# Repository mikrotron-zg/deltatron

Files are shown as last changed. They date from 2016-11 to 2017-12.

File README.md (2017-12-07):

# Deltatron v1.1
Deltatron is Kossel Mini RepRap 3D Printer variant by [DIYkits.eu](http://www.diykits.eu/). This is version 1.1 of Deltatron in which we switched from J-Head to E3D v6 Lite hotend. For other versions please check _Git tags_ or _GitHub releases_.

This repository includes all 3D printable parts, Marlin firmware ready for upload, and last but not least - assembly and user manuals in Croatian and (eventually) in English.

**New in version 1.1:**
* E3D v6 Lite hotend instead of J-Head
* changed hotend mount, print cooling fan mount and z-probe models to fit new hotend
* changed bed bracket and ramps bracket models, added support for models where needed
* updated assembly manual and added assembly manual for E3D Lite hotend (both in Croatian only)
* changed Configuration.h in Marlin firmware to reflect the hardware changes

## --- **Croatian**

Deltatron je varijanta Kossel Mini RepRap 3D printera - kit možete kupiti u [DIYkits.eu web dućanu](http://www.diykits.eu/shophr/). Ovo je verzija 1.1 Deltatron kita, koja umjesto J-Heada koristi E3D v6 Lite ispisnu glavu (hotend). Starije verzije dostupne su putem _Git tagova_ ili u GitHub repozitoriju pod _releases_.

U ovom repozitoriju nalaze se 3D modeli svih dijelova koji se mogu isprintati 3D printerom, Marlin firmware prilagođen ovome kitu, kao i upute za sastavljanje i korištenje Deltatrona na hrvatskom.

**Novosti u verziji 1.1:**
* J-Head ispisna glava zamjenjena je za E3D v6 Lite hotend
* izmjenjeni modeli za pričvršćenje hotenda, ventilatora za hlađenje printa i z probe
* izmjenjeni modeli držača elektronike i podloge za printanje, gdje je bilo potrebno dodana je potpora za 3D print u modele
* ažurirane su upute za sastavljanje Deltatrona i dodane su upute za sastavljenje E3D Lite6 hotenda
* promjenjene postavke u Configuration.h datoteci Marlin firmware-a u skladu s hardverskim izmjenama

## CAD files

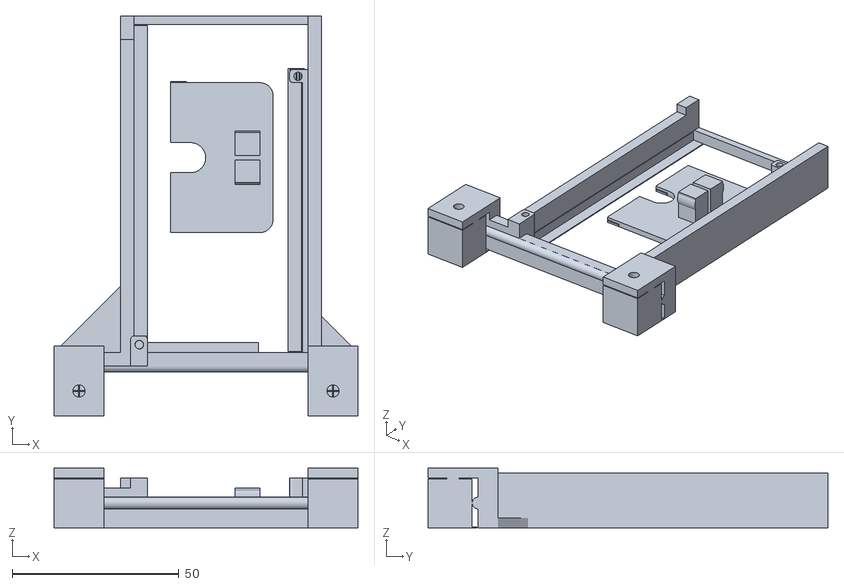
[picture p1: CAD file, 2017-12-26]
model/plate04_support.stl
91.2 x 120.0 x 18.0

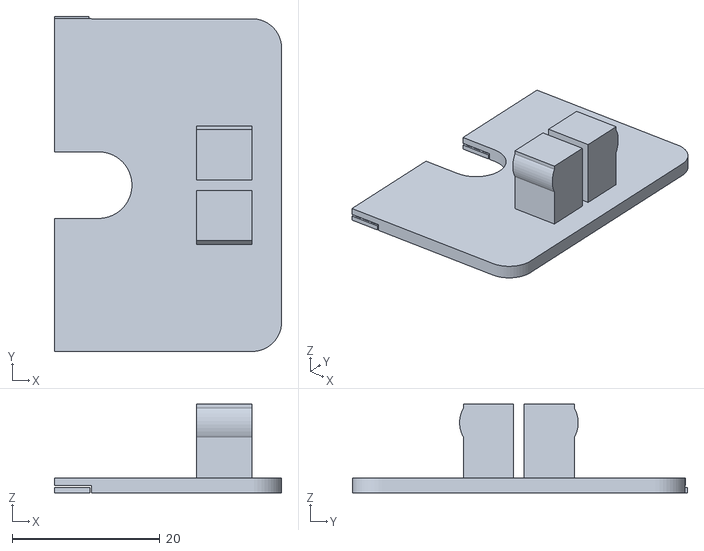
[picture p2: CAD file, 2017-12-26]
model/connector_plate_power.stl
30.8 x 45.3 x 12.0

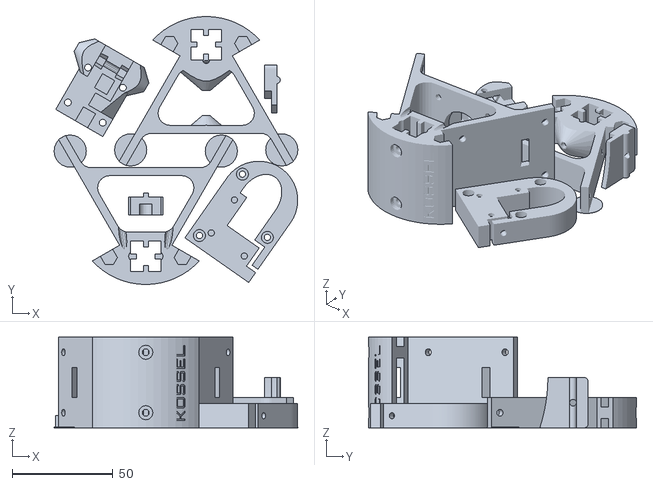
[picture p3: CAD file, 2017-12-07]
model/plate03_3x.stl
121.0 x 133.0 x 45.0

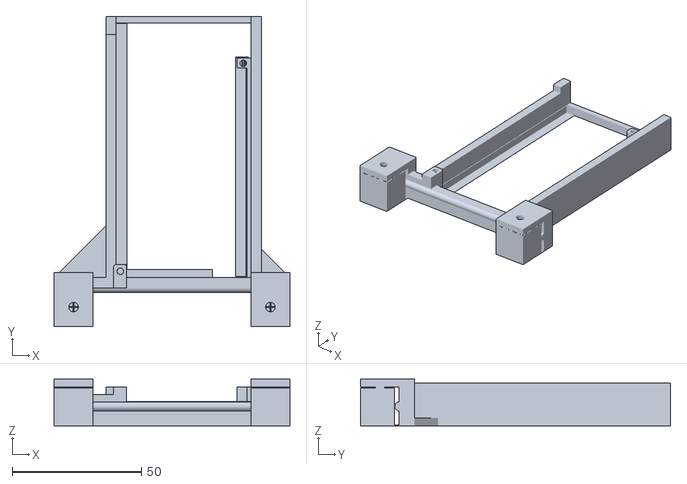
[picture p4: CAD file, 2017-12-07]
model/ramps_bracket.stl
91.2 x 120.0 x 18.0

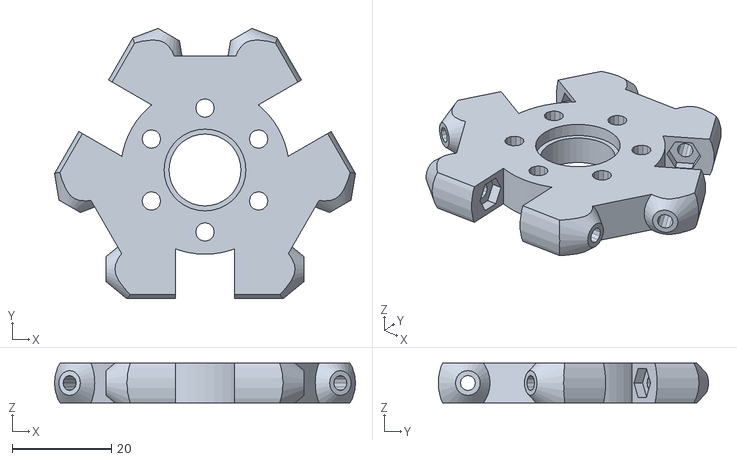
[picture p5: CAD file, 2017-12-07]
model/effector.stl
60.7 x 54.5 x 8.00

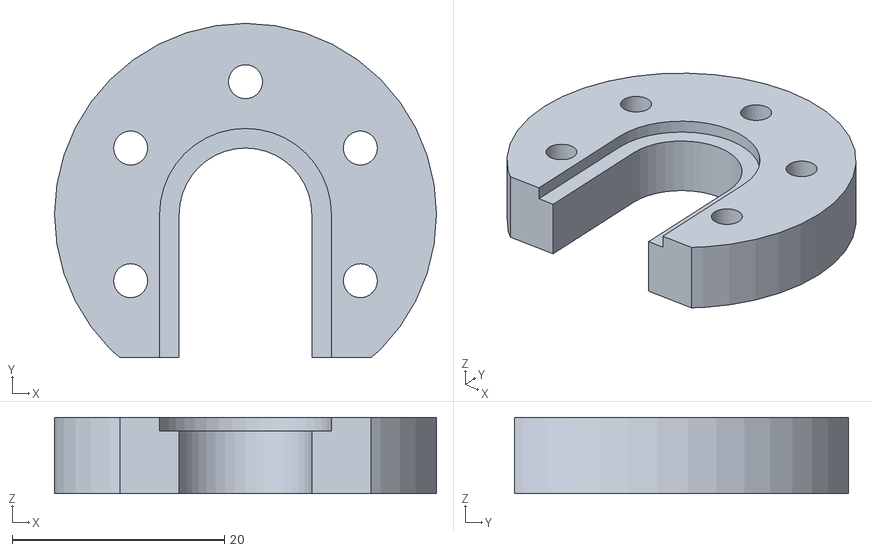
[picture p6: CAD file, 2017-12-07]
model/groove_mount.stl
36.0 x 31.5 x 7.20

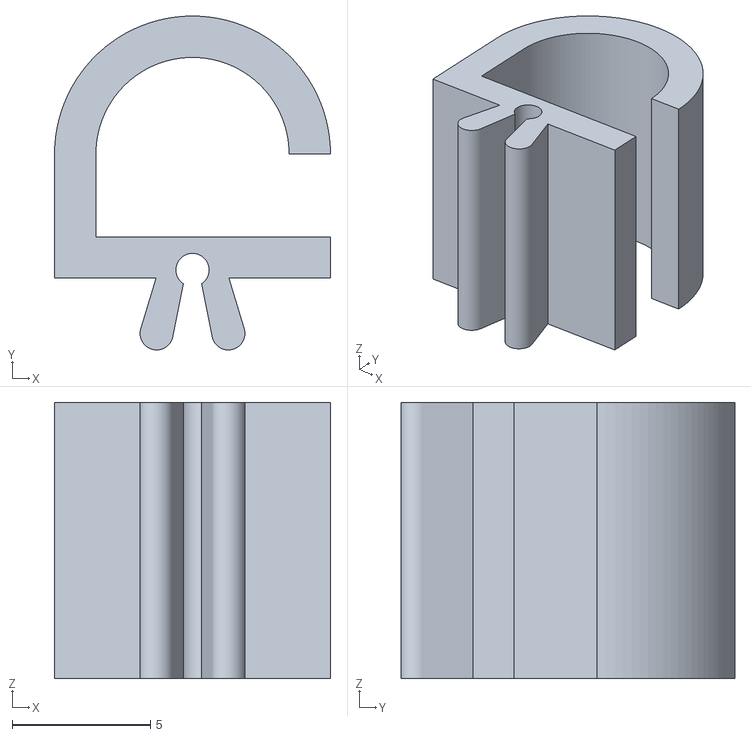
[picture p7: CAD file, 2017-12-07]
model/hook_clip.stl
10.0 x 12.1 x 10.0

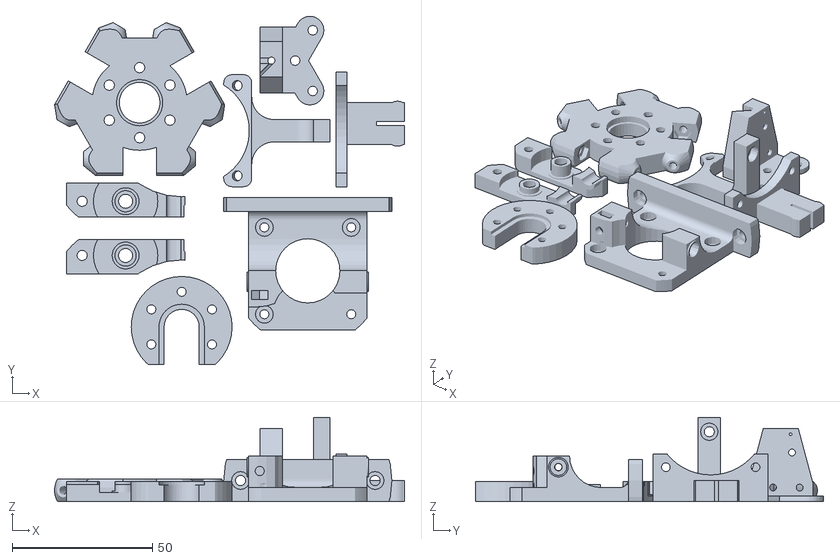
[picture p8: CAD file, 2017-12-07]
model/plate01_1x.stl
124.9 x 124.3 x 30.0

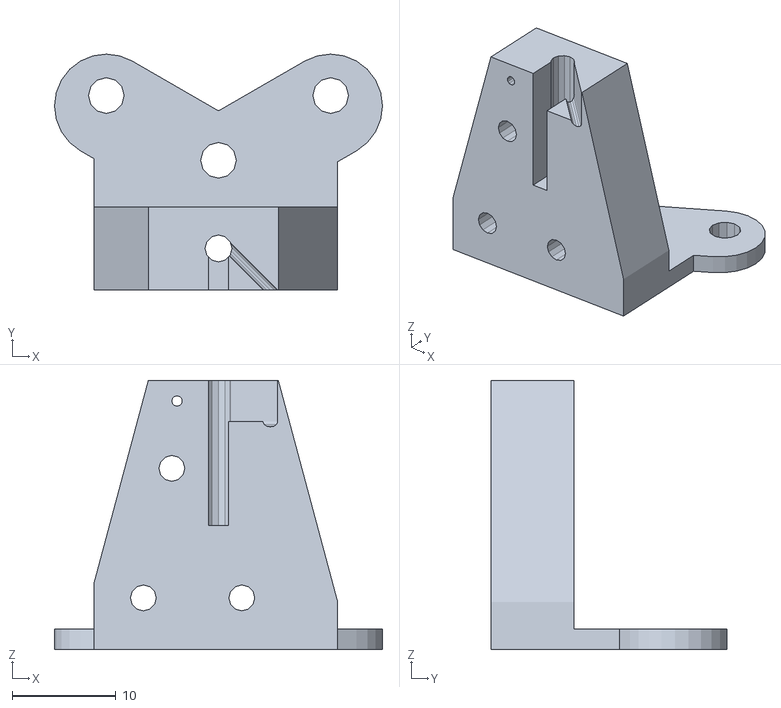
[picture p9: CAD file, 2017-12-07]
model/retractable.stl
31.7 x 22.8 x 26.0

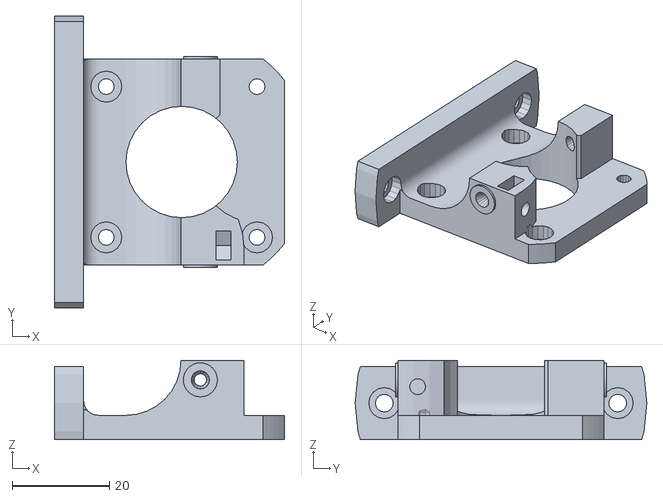
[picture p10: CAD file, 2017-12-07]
model/compact_direct_drive_extruder_base.stl
47.3 x 60.0 x 16.3

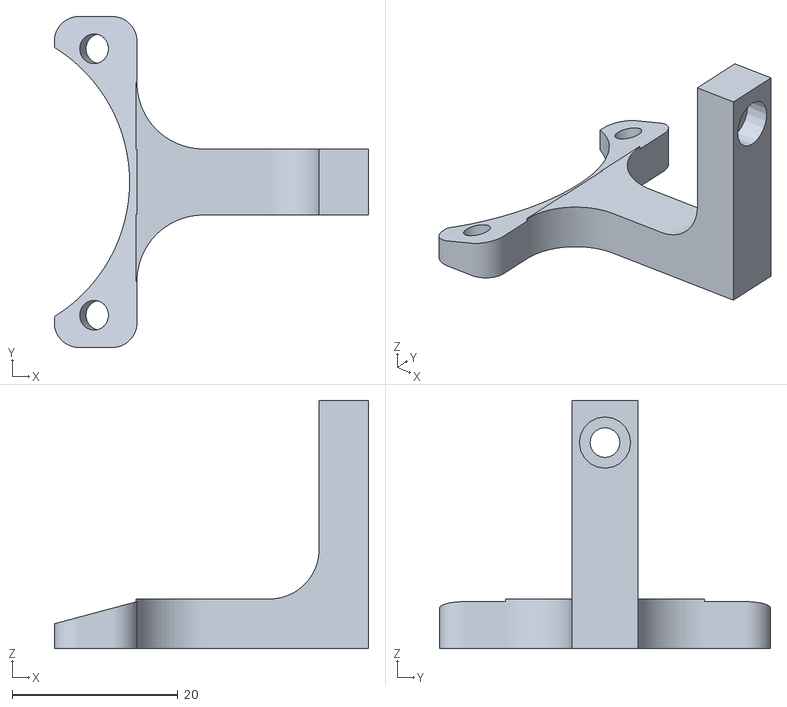
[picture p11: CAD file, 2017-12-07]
model/part_cooling_fan_mount.stl
38.0 x 40.0 x 30.0

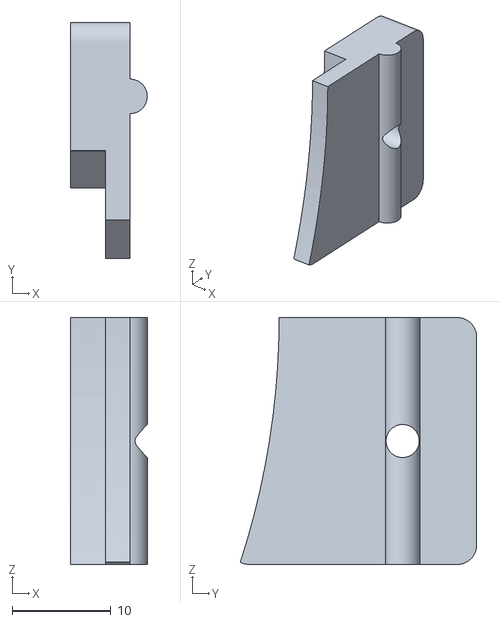
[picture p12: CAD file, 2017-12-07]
model/bed_bracket.stl
7.75 x 23.9 x 25.0

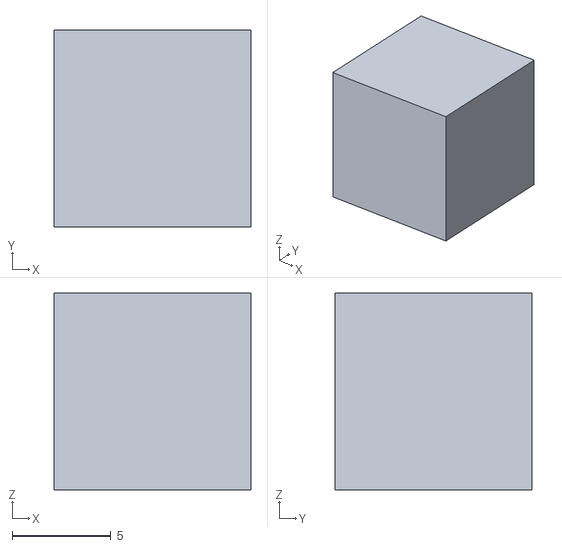
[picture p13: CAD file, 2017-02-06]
model/test_cube.stl
10.0 x 10.0 x 10.0

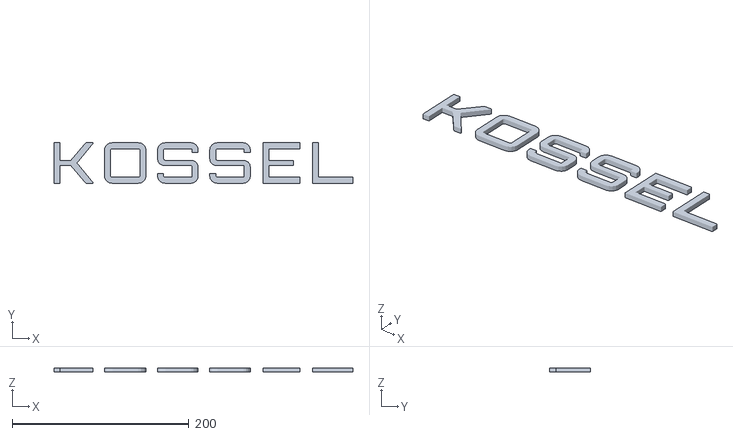
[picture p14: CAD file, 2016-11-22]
model/logotype.stl
338.0 x 46.0 x 5.00

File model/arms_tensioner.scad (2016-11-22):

//Arms tensioner for Mini Kossel

width=2;       //tensioner width
height=10;      //tensioner height
armspan=38.2;   //kossel arms span
tension=25;    //how much to make tensioner smaller than arms span
arc_dia=5;    //arc inner diameter
$fn=40;

main();

module main(){
    union(){
        translate([arc_dia/2, -width/2,0]) cube([armspan-tension, width, height]);
        rotate([0,0,-90]) arc();
        translate([arc_dia + armspan - tension, 0, 0]) arc();
    }
}

module arc(){
    difference(){
        cylinder(d=arc_dia + 2*width, h=height);
        cylinder(d=arc_dia, h=height);
        translate([-arc_dia/2 - width, 0, 0]) cube([0 + 2*width, arc_dia/2 + width, height]);
    }
}

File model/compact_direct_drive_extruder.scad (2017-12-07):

// Compact direct drive bowden extruder for 1.75mm filament
// Licence: CC BY-SA 3.0, http://creativecommons.org/licenses/by-sa/3.0/
// Author: Dominik Scholz <schlotzz@schlotzz.com> and contributors
// Using MK8 style hobbed pulley 13x8mm from: https://www.reprapsource.com/en/show/6889
// visit: http://www.schlotzz.com
// changed: 2014-04-04, added idler slot and funnel on bowden side for easier filament insertion
// changed: 2014-04-27, placed base and idler "printer ready"
// changed: 2014-09-22, fixed non-manifold vertexes between base and filament tunnel
// changed: 2014-11-13, added bowden inlet
// changed: 2015-03-17, updated idler for better MK7 drive gear support
// changed: 2015-10-13, designed alternative idler to solve breaking of bearing support


/*
	design goals:
	- use 13x8mm hobbed pulley (mk8) or 13x12mm (mk7)
	- filament diameter parametric (1.75mm or 3mm)
	- use 608zz bearing
	- use M5 push fit connector
*/

// avoid openscad artefacts in preview
epsilon = 0.01;

// increase this if your slicer or printer make holes too tight
extra_radius = 0.2; //was 0.1

// major diameter of metric 3mm thread
m3_major = 2.85;
m3_radius = m3_major / 2 + extra_radius;
m3_wide_radius = m3_major / 2 + extra_radius + 0.2;

// diameter of metric 3mm hexnut screw head
m3_head_radius = 3 + extra_radius;

// drive gear
drive_gear_outer_radius = 8.00 / 2;
drive_gear_hobbed_radius = 6.35 / 2;
drive_gear_hobbed_offset = 3.2;
drive_gear_length = 13;
drive_gear_tooth_depth = 0.2;

// base width for frame plate
base_width = 15;
base_length = 60;
base_height = 5;

// nema 17 dimensions
nema17_width = 42.3;
nema17_hole_offsets = [
	[-15.5, -15.5, 1.5],
	[-15.5,  15.5, 1.5],
	[ 15.5, -15.5, 1.5],
	[ 15.5,  15.5, 1.5 + base_height]
];

// inlet type
inlet_type = 0; // 0:normal, 1:push-fit


// filament
filament_diameter = 1.75; // 1.75, 3.00
filament_offset = [
	drive_gear_hobbed_radius + filament_diameter / 2 - drive_gear_tooth_depth,
	0,
	base_height + drive_gear_length - drive_gear_hobbed_offset - 2.5
];





// helper function to render a rounded slot
module rounded_slot(r = 1, h = 1, l = 0, center = false)
{
	hull()
	{
		translate([0, -l / 2, 0])
			cylinder(r = r, h = h, center = center);
		translate([0, l / 2, 0])
			cylinder(r = r, h = h, center = center);
	}
}


// mounting plate for nema 17
module nema17_mount()
{
	// settings
	width = nema17_width;
	height = base_height;
	edge_radius = 27;
	axle_radius = drive_gear_outer_radius + 1 + extra_radius;

	difference()
	{
		// base plate
		translate([0, 0, height / 2])
			intersection()
			{
				cube([width, width, height], center = true);
				cylinder(r = edge_radius, h = height + 2 * epsilon, $fn = 128, center = true);
			}
		
		// center hole
		translate([0, 0, -epsilon]	)
			cylinder(r = 11.25 + extra_radius, h = base_height + 2 * epsilon, $fn = 32);

		// axle hole
		translate([0, 0, -epsilon])
			cylinder(r = axle_radius, h = height + 2 * epsilon, $fn = 32);

		// mounting holes
		for (a = nema17_hole_offsets)
			translate(a)
			{
				cylinder(r = m3_radius, h = height * 4, center = true, $fn = 16);
				cylinder(r = m3_head_radius, h = height + epsilon, $fn = 16);
			}
	}
}


// plate for mounting extruder on frame
module frame_mount()
{
	// settings
	width = base_width;
	length = base_length;
	height = base_height+1;
	hole_offsets = [
		[0,  length / 2 - 6, 3.5],
		[0, -length / 2 + 6, 3.5]
	];
	corner_radius = 3;

	difference()
	{
		// base plate
		intersection()
		{
			union()
			{
				translate([0, 0, height / 2])
					cube([width, length, height], center = true);
				translate([base_width / 2 - base_height / 2 - corner_radius / 2, 0, height + corner_radius / 2])
					cube([base_height + corner_radius, nema17_width, corner_radius], center = true);
				translate([base_width / 2 - base_height / 2, 0, 6])
					cube([base_height, nema17_width, 12], center = true);
			}

			cylinder(r = base_length / 2, h = 100, $fn = 32);
		}

		// rounded corner
		translate([base_width / 2 - base_height - corner_radius, 0, height + corner_radius])
			rotate([90, 0, 0])
				cylinder(r = corner_radius, h = nema17_width + 2 * epsilon, center = true, $fn = 32);

		// mounting holes
		for (a = hole_offsets)
			translate(a)
			{
				cylinder(r = m3_wide_radius, h = height * 2 + 2 * epsilon, center = true, $fn = 16);
				cylinder(r = m3_head_radius, h = height + epsilon, $fn = 16);
			}

		// nema17 mounting holes
		translate([base_width / 2, 0, nema17_width / 2 + base_height])
			rotate([0, -90, 0])
			for (a = nema17_hole_offsets)
				translate(a)
				{
					cylinder(r = m3_radius, h = height * 4, center = true, $fn = 16);
					cylinder(r = m3_head_radius, h = height + epsilon, $fn = 16);
				}
	}
}


// inlet for filament
module filament_tunnel()
{
	// settings
	width = 8;
	length = nema17_width;
	height = filament_offset[2] - base_height + 4;

	translate([0, 0, height / 2])
	{
		difference()
		{
			union()
			{
				// base
				translate([-height / 2, 0, 0])
					cube([width + height, length, height], center = true);

				// inlet strengthening
				translate([0, -length / 2, -height / 2 + filament_offset[2] - base_height])
					rotate([90, 0, 0])
						cylinder(r = 3.5, h = 1, center = true, $fn = 32);

				// outlet strengthening
				translate([0, length / 2, -height / 2 + filament_offset[2] - base_height])
					rotate([90, 0, 0])
						cylinder(r = 3.5, h = 1, center = true, $fn = 32);

				// idler tensioner
				intersection()
				{
					translate([5, -length / 2 + 8, 0])
						cube([width, 16, height], center = true);
					translate([-17.8, -20 ,0])
						cylinder(r = 27, h = height + 2 * epsilon, center = true, $fn = 32);
				}

			}

			// middle cutout for drive gear
			translate([-filament_offset[0], 0, 0])
				cylinder(r = 11.25 + extra_radius, h = height + 2 * epsilon, center = true, $fn = 32);

			// middle cutout for idler
			translate([11 + filament_diameter / 2, 0, 0])
				cylinder(r = 12.5, h = height + 2 * epsilon, center = true, $fn = 32);

			// idler mounting hexnut
			translate([filament_diameter + 1, -nema17_width / 2 + 4, .25])
				rotate([0, 90, 0])
					cylinder(r = m3_radius, h = 50, center = false, $fn = 32);
			translate([filament_diameter + 3, -nema17_width / 2 + 4, 5])
				cube([2.5 + 3 * extra_radius, 5.5 + 2.5 * extra_radius, 10], center = true);
			translate([filament_diameter + 3, -nema17_width / 2 + 4, 0])
				rotate([0, 90, 0])
					cylinder(r = 3.15 + 2.5 * extra_radius, h = 2.5 + 3 * extra_radius, center = true, $fn = 6);
			
			// rounded corner
			translate([-height - width / 2, 0, height / 2])
				rotate([90, 0, 0])
					cylinder(r = height, h = length + 2 * epsilon, center = true, $fn = 32);
			
			// funnnel inlet
			if (inlet_type == 0)
			{
				// normal type
				translate([0, -length / 2 + 1 - epsilon, -height / 2 + filament_offset[2] - base_height])
					rotate([90, 0, 0])
						cylinder(r1 = filament_diameter / 2, r2 = filament_diameter / 2 + 1 + epsilon / 1.554,
							h = 3 + epsilon, center = true, $fn = 16);
			}
			else
			{
				// inlet push fit connector m5 hole
				translate([0, -length / 2 - 1 + 2.5 + epsilon, -height / 2 + filament_offset[2] - base_height])
					rotate([90, 0, 0])
						cylinder(r = 2.25, h = 5 + 2 * epsilon, center = true, $fn = 16);

				// funnel inlet outside
				translate([0, -length / 2 + 4, -height / 2 + filament_offset[2] - base_height])
					rotate([90, 0, 0])
						cylinder(r1 = filament_diameter / 2, r2 = filament_diameter / 2 + 1,
							h = 2, center = true, $fn = 16);

			}

			// funnnel outlet inside
			translate([0, 12, -height / 2 + filament_offset[2] - base_height])
				rotate([90, 0, 0])
					cylinder(r1 = filament_diameter / 2, r2 = filament_diameter / 2 + 1.25,
						h = 8, center = true, $fn = 16);

			// outlet push fit connector m6 hole
			translate([0, length / 2 + 1 - 2.5 + epsilon, -height / 2 + filament_offset[2] - base_height])
				rotate([90, 0, 0])
					cylinder(r = 3, h = 5 + 2 * epsilon, center = true, $fn = 16);

			// funnel outlet outside
			translate([0, length / 2 - 4, -height / 2 + filament_offset[2] - base_height])
				rotate([90, 0, 0])
					cylinder(r1 = filament_diameter / 2 + 1, r2 = filament_diameter / 2,
						h = 2, center = true, $fn = 16);

			// filament path
			translate([0, 0, -height / 2 + filament_offset[2] - base_height])
				rotate([90, 0, 0])
					cylinder(r = filament_diameter / 2 + 2 * extra_radius,
						h = length + 2 * epsilon, center = true, $fn = 16);
			
			// screw head inlet
			translate(nema17_hole_offsets[2] - [filament_offset[0], 0, height / 2 + 1.5])
				sphere(r = m3_head_radius, $fn = 16);
		}
	}
}


// render drive gear
module drive_gear()
{
	r = drive_gear_outer_radius - drive_gear_hobbed_radius;
	rotate_extrude(convexity = 10)
	{
		difference()
		{
			square([drive_gear_outer_radius, drive_gear_length]);
			translate([drive_gear_hobbed_radius + r, drive_gear_length - drive_gear_hobbed_offset])
				circle(r = r, $fn = 16);
		}
	}
}
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

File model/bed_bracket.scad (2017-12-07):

// Bed bracket for Deltatron by Mikrotron d.o.o.

use <chamfers.scad>;

// smoothing of curves
$fn = 50;

// extra dimension to remove ambiguity of walls
ex = 0.10;

// aluminium extrusion dimension
profile = 15;
profile_gap = 3.6; // frame groove width

// screw dimensions
screw_3x8_cap_dia = 5.7;
screw_3x8_cap_height = 3.2;

bed_dia = 170; // glass bed diameter
bed_overlap = 2; // glass bed overlap with the alu profile
bed_dia2 = 160; // lower bed cutoff

wall = 6;
bracket_width = 25;
bracket_thickness = 2.5;

// ENTRY POINT

bed_bracket();

module bed_bracket(){
    translate([0, 0, bracket_width]) rotate([0, -90, 0]) {
        translate([-bed_dia/2, 0, -profile]) %frame();
        difference(){
            translate([-bracket_width, profile, 0]) draw_bracket();
            translate([0, -bed_dia/2 + bed_overlap, bracket_thickness]) 
                glass_bed(bed_dia,4);
            translate([0, -bed_dia/2, -ex]) 
                glass_bed(bed_dia2, bracket_thickness + 2*ex);
        }
    }
}

module draw_bracket(){
    
    
    bracket_length = 25; // will be cut off to fit to frame
    
    translate([0, 0, wall]) rotate([180, 0, 0]) difference(){
            difference(){
            union(){
                rounded_rect(bracket_width, bracket_length, wall, 2);
                translate([0, profile/2, wall]) slider();
            }
        }
        
        // screw hole
        translate([bracket_width/2, profile/2, -ex]) {
            cylinder(d = screw_3x8_cap_dia/2 + 0.5, h = wall+2);
            cylinder(d = screw_3x8_cap_dia + 0.5, h = wall/2 + ex);
        }
    }
    
}

module slider(slider_length = bracket_width){
    // part that slides in frame groove
    difference(){
        rotate([0,90,0]) cylinder(d = profile_gap - ex, h = slider_length);
        translate([-ex, -profile_gap/2 - 2*ex, -profile_gap/2 - 2*ex])
            cube([slider_length + 2*ex, profile_gap + 2*ex, profile_gap/2 + 2*ex]);
    }
}


// NON-PRINTED PARTS

module frame(profile_length = bed_dia){
    // draws basic aluminium extrusion frame
    difference(){
        cube([profile_length, profile, profile]);
        translate([-ex, profile/2 - profile_gap/2, profile - profile_gap])
            cube([profile_length + 2*ex, profile_gap, profile_gap + ex]);
        translate([-ex, profile - profile_gap, profile/2 - profile_gap/2])
            cube([profile_length + 2*ex, profile_gap + ex, profile_gap]);
        translate([-ex, -ex, profile/2 - profile_gap/2])
            cube([profile_length + 2*ex, profile_gap + ex, profile_gap]);
        translate([-ex, profile/2 - profile_gap/2, -ex])
            cube([profile_length + 2*ex, profile_gap, profile_gap + ex]);
    }
}

module glass_bed(dia, thickness){
    cylinder(d = dia, h = thickness, $fn = 200);
}

//UTILITY

//draws a rounded rectangle
module rounded_rect(x, y, z, radius = 1) {
    translate([radius,radius,0]) //move origin to outer limits
	linear_extrude(height=z)
		minkowski() {
			square([x-2*radius,y-2*radius]); //keep outer dimensions given by x and y
			circle(r = radius, $fn=100);
		}
}

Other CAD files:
model/arms_tensioner.stl
model/clip.stl
model/frame_motor.stl
model/frame_top.stl
model/chamfers.scad
model/carriage.scad
model/carriage.stl
model/clip.scad
model/compact_direct_drive_extruder_idler_alternative.stl
model/configuration.scad
model/connector_plate.scad
model/connector_plate_usb.stl
model/effector.scad
model/endstop.scad
model/endstop.stl
model/fan_mount.scad
model/fan_mount.stl
model/frame_motor.scad
model/frame_top.scad
model/groove_mount.scad
model/logotype.scad
model/microswitch.scad
model/nema17.scad
model/part_cooling_fan_mount.scad
model/plate01_1x.scad
model/plate02_1x.scad
model/plate02_1x.stl
model/plate03_3x.scad
model/plate04_support.scad
model/ramps_bracket.scad
model/ramps_fan_mount.scad
model/ramps_fan_mount.stl
model/retractable.scad
model/test_cube.scad
model/vertex.scad
model/vertical_carriage_base.scad
model/vertical_carriage_base.stl

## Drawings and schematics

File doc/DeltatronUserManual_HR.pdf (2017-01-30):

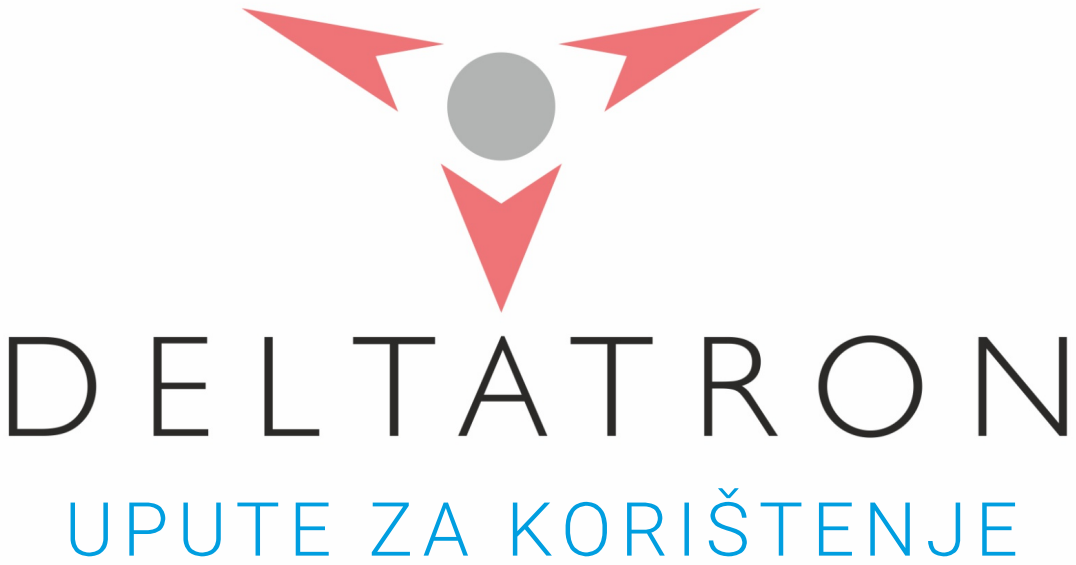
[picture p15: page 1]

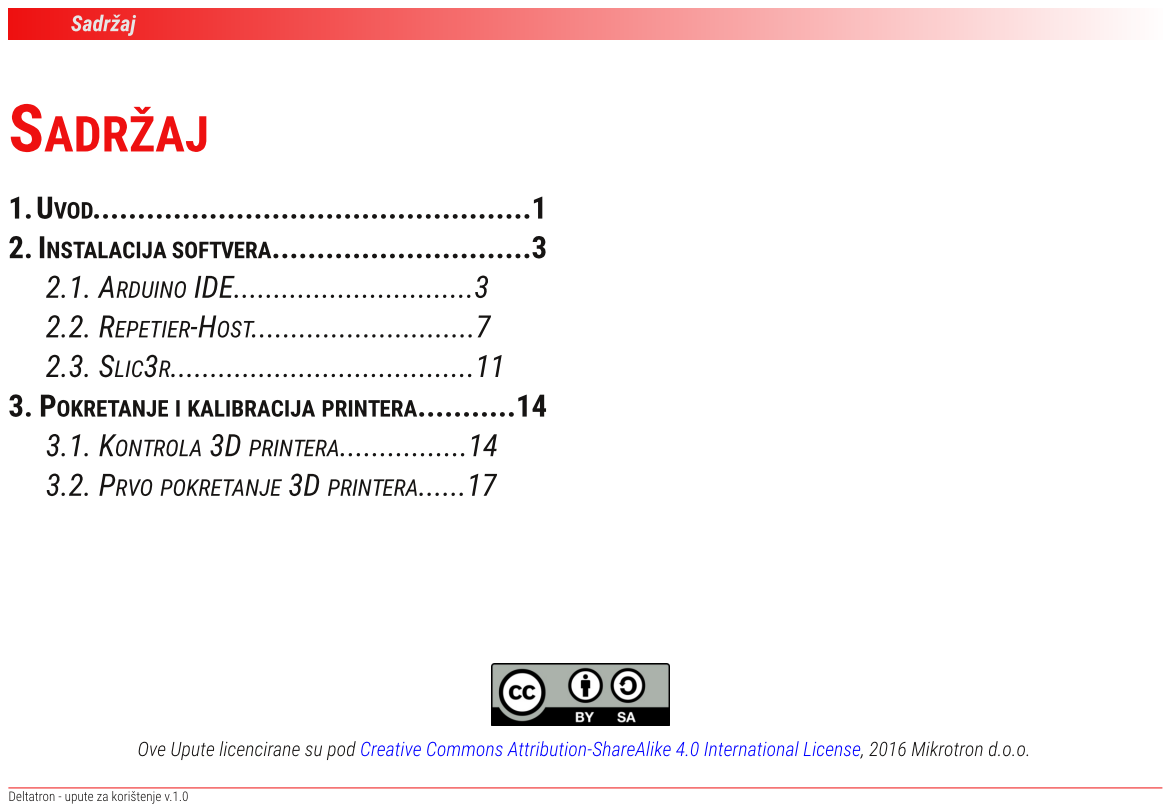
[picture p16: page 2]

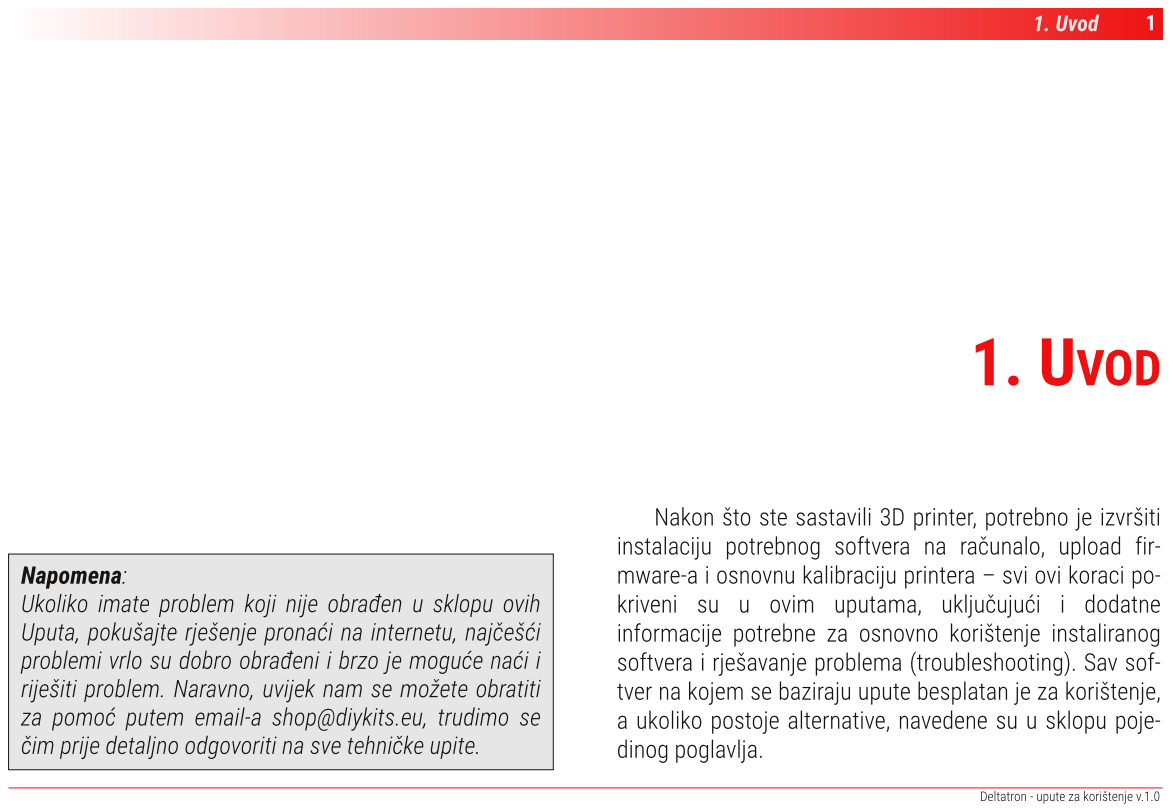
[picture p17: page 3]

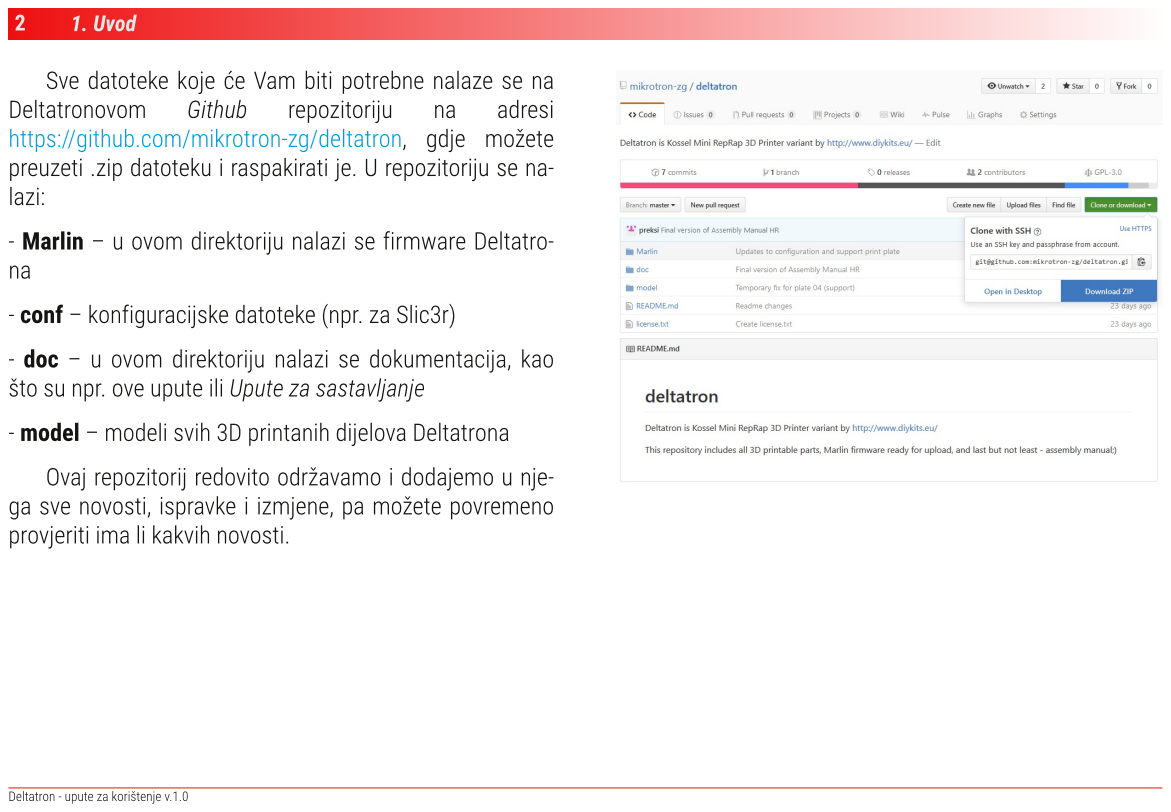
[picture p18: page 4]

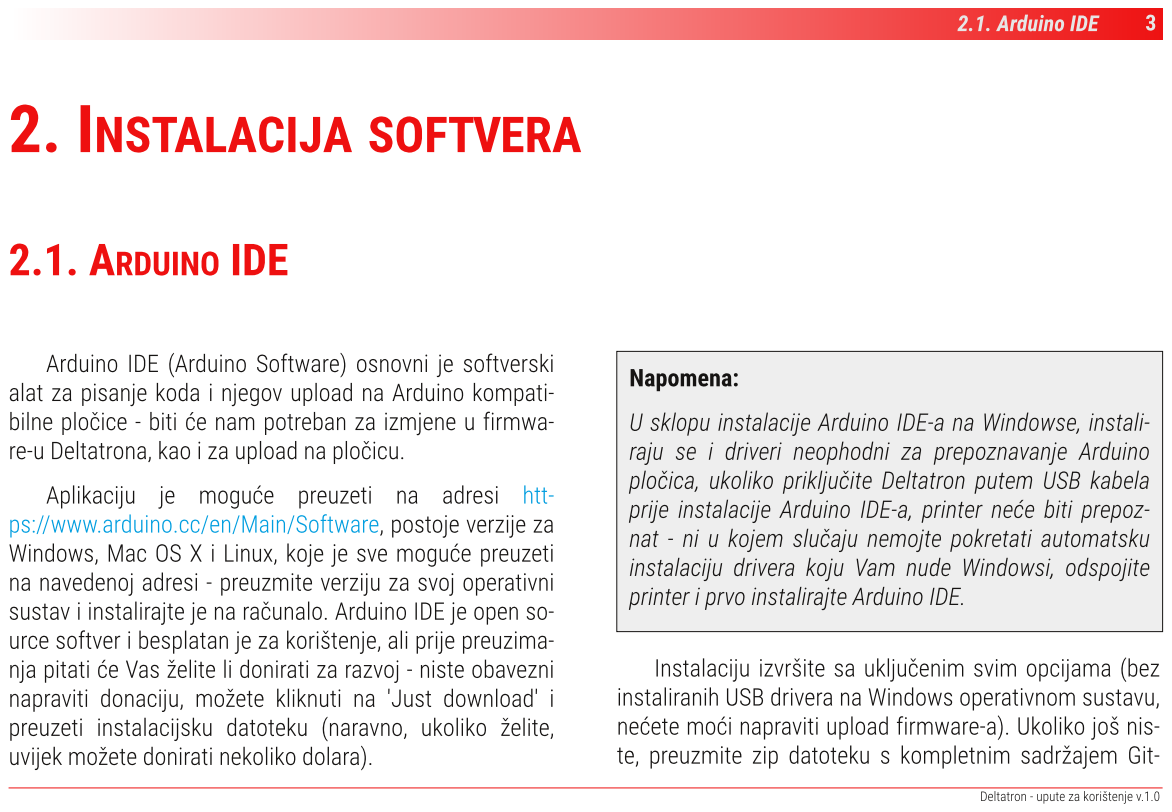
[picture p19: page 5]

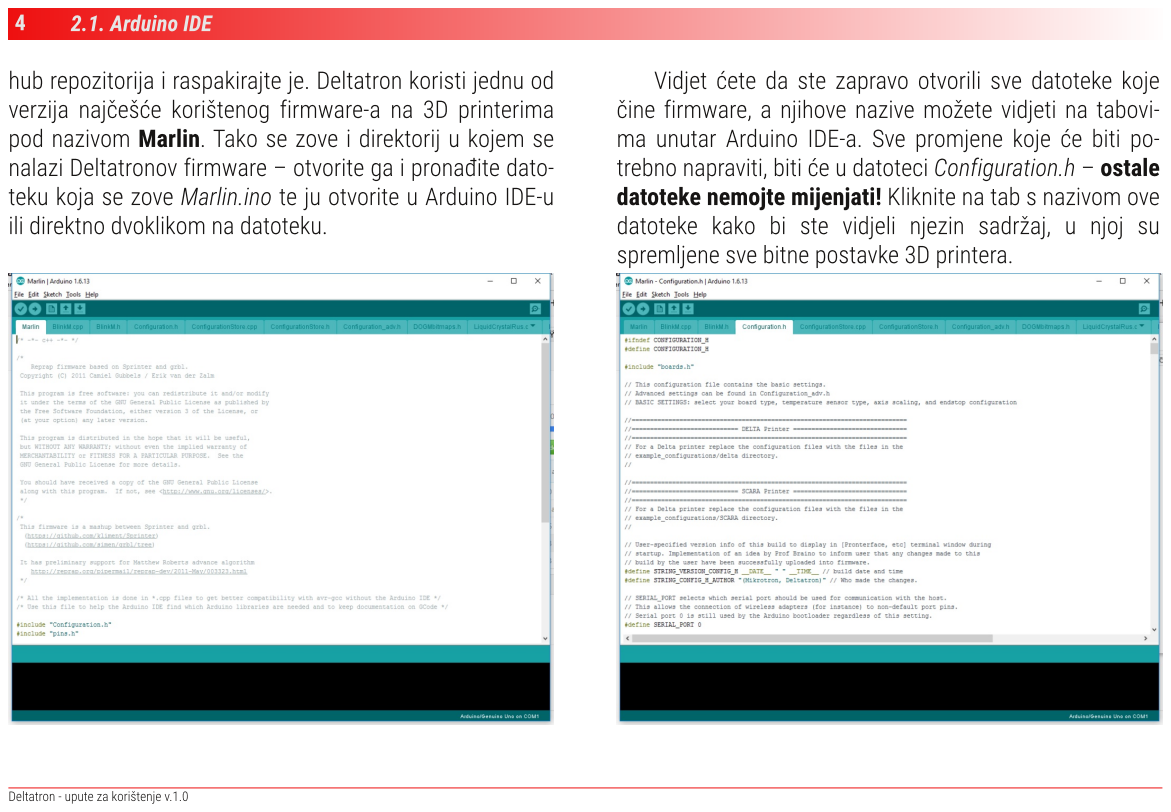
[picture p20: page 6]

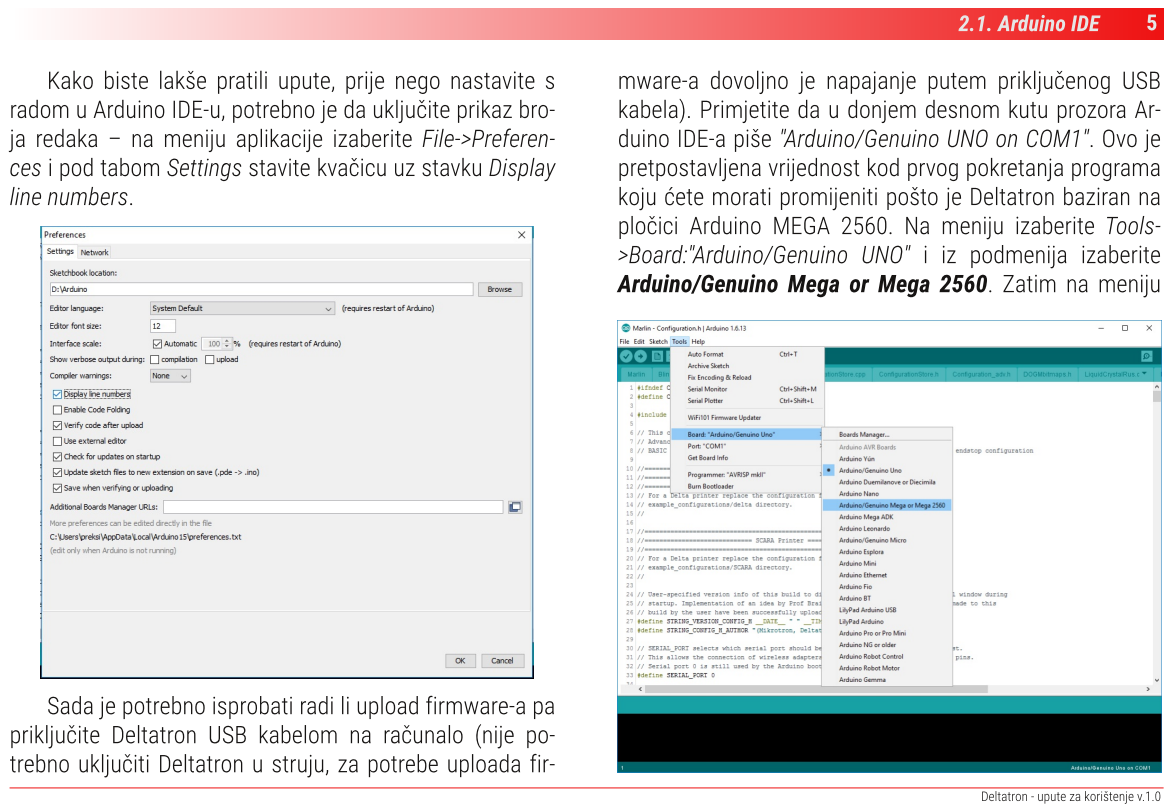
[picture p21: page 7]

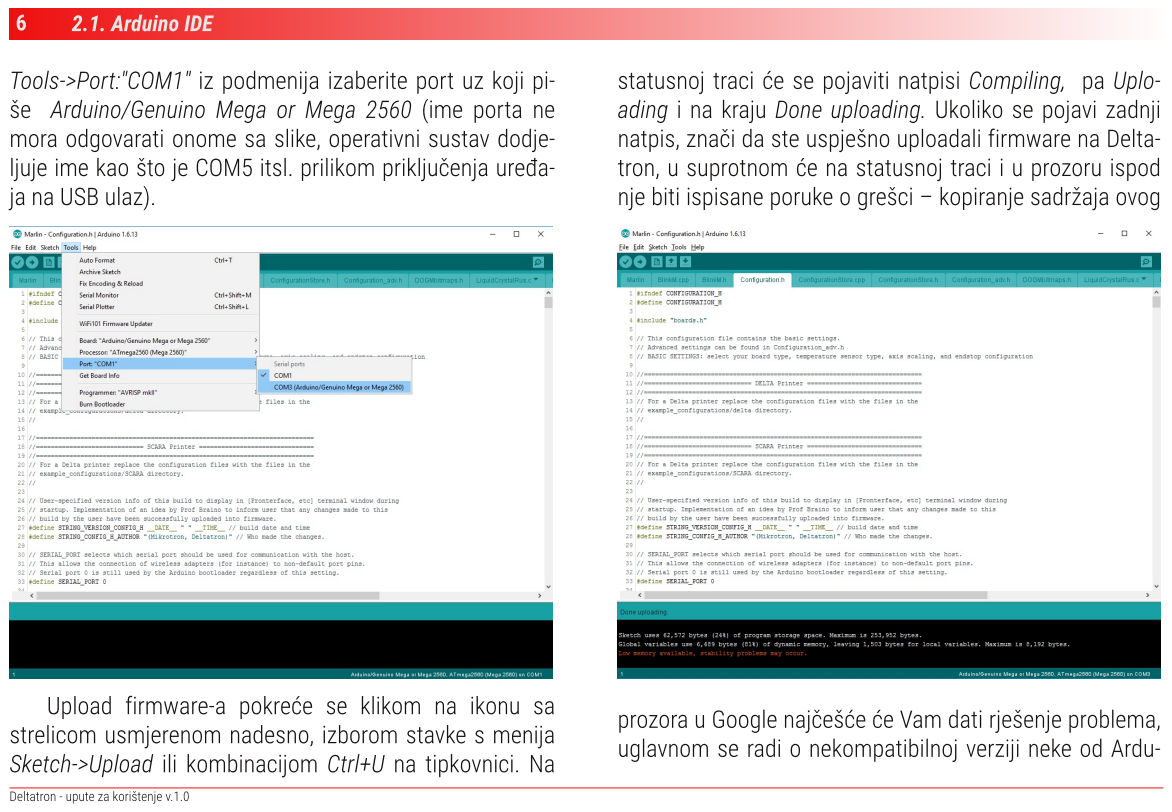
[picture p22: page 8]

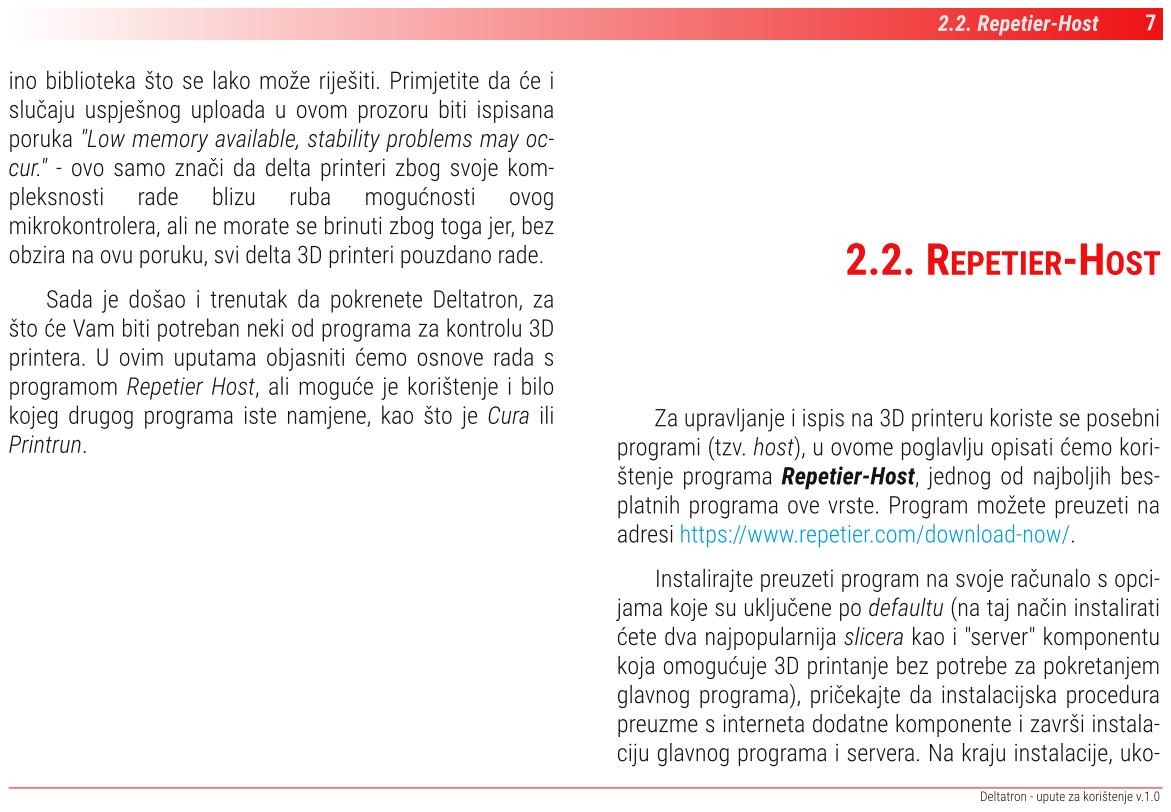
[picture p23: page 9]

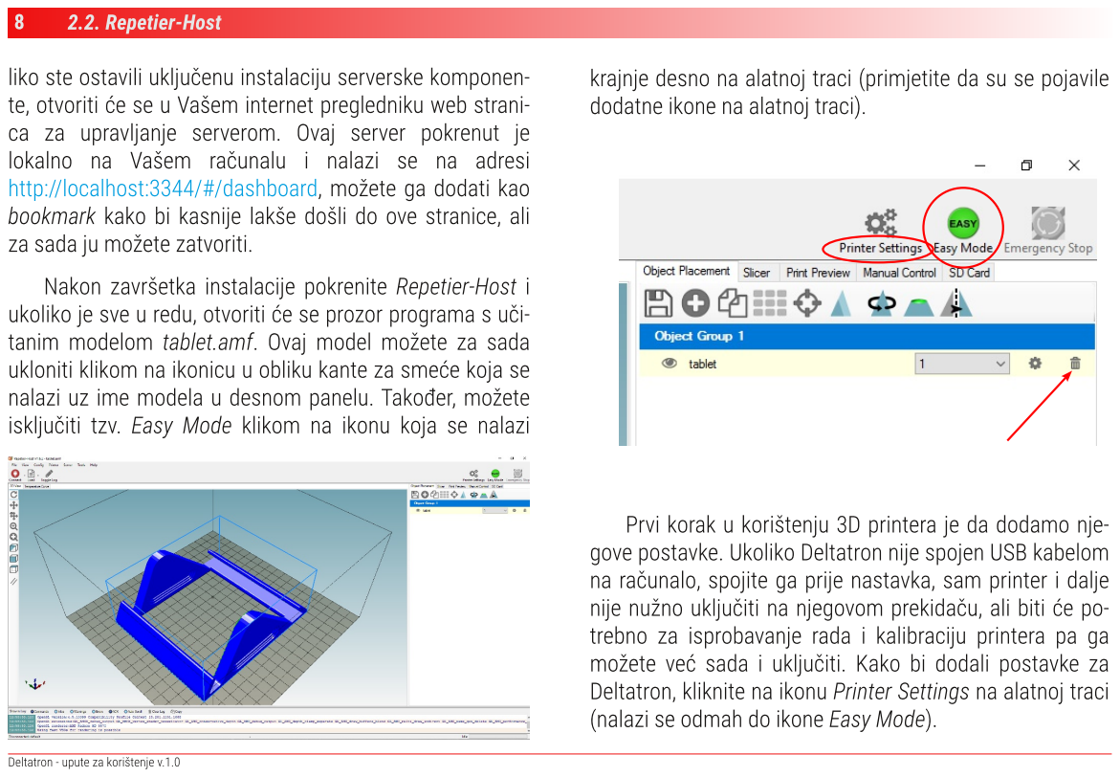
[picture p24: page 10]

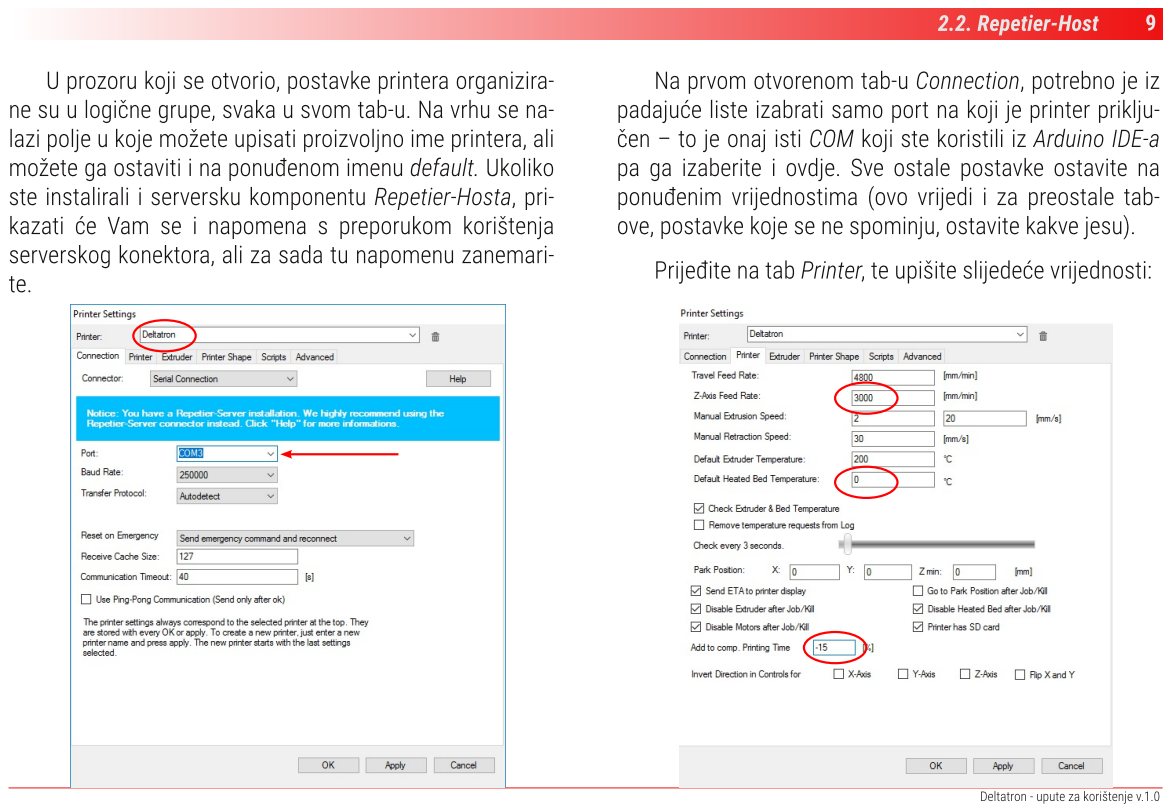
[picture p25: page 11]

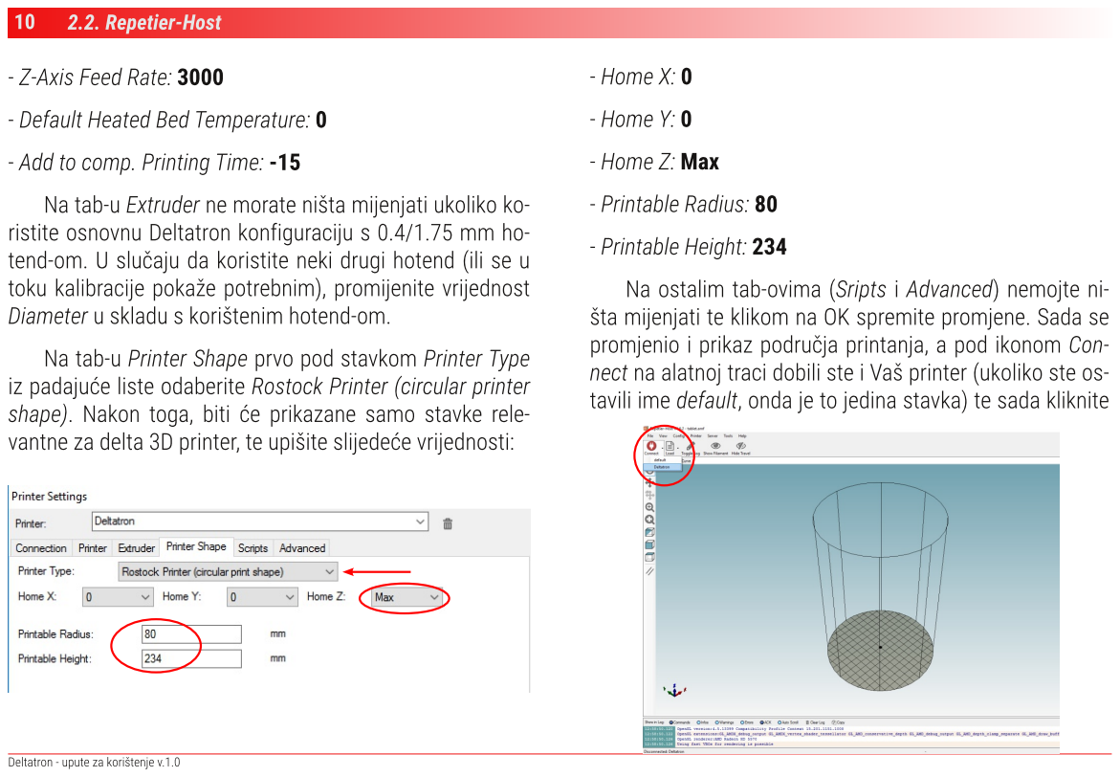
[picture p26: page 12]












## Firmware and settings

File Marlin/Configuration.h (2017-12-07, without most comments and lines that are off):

#define CONFIGURATION_H
#include "boards.h"
#define STRING_VERSION_CONFIG_H __DATE__ " " __TIME__ // build date and time
#define STRING_CONFIG_H_AUTHOR "(Mikrotron, Deltatron)" // Who made the changes.
#define SERIAL_PORT 0
#define BAUDRATE 250000 //Windows 250000, Linux 115200
  #define MOTHERBOARD BOARD_RAMPS_13_EFB
#define CUSTOM_MENDEL_NAME "Deltatron"
#define EXTRUDERS 1
#define POWER_SUPPLY 1
#define DELTA
#define DELTA_SEGMENTS_PER_SECOND 160
#define DELTA_DIAGONAL_ROD 228.0 // mm
#define DELTA_SMOOTH_ROD_OFFSET 163.33 // mm
#define DELTA_EFFECTOR_OFFSET 30.0 // mm
#define DELTA_CARRIAGE_OFFSET 26.0 // mm WAS 30.0, 26.75
#define DELTA_RADIUS (DELTA_SMOOTH_ROD_OFFSET-DELTA_EFFECTOR_OFFSET-DELTA_CARRIAGE_OFFSET)
#define DELTA_PRINTABLE_RADIUS 80.0
#define SIN_60 0.8660254037844386
#define COS_60 0.5
#define DELTA_TOWER1_X -SIN_60*DELTA_RADIUS // front left tower
#define DELTA_TOWER1_Y -COS_60*DELTA_RADIUS
#define DELTA_TOWER2_X SIN_60*DELTA_RADIUS // front right tower
#define DELTA_TOWER2_Y -COS_60*DELTA_RADIUS
#define DELTA_TOWER3_X 0.0 // back middle tower
#define DELTA_TOWER3_Y DELTA_RADIUS
#define DELTA_DIAGONAL_ROD_2 pow(DELTA_DIAGONAL_ROD,2)
#define TEMP_SENSOR_0 5
#define TEMP_SENSOR_1 0
#define TEMP_SENSOR_2 0
#define TEMP_SENSOR_BED 0
#define MAX_REDUNDANT_TEMP_SENSOR_DIFF 10
#define TEMP_RESIDENCY_TIME 10  // (seconds)
#define TEMP_HYSTERESIS 3       // (degC) range of +/- temperatures considered "close" to the target one
#define TEMP_WINDOW     1       // (degC) Window around target to start the residency timer x degC early.
#define HEATER_0_MINTEMP 5
#define HEATER_1_MINTEMP 5
#define HEATER_2_MINTEMP 5
#define BED_MINTEMP 5
#define HEATER_0_MAXTEMP 275
#define HEATER_1_MAXTEMP 275
#define HEATER_2_MAXTEMP 275
#define BED_MAXTEMP 130
#define PIDTEMP
#define BANG_MAX 255 // limits current to nozzle while in bang-bang mode; 255=full current
#define PID_MAX 255 // limits current to nozzle while PID is active (see PID_FUNCTIONAL_RANGE below); 255=full current
  #define PID_FUNCTIONAL_RANGE 10 // If the temperature difference between the target temperature and the actual temperature
  #define PID_INTEGRAL_DRIVE_MAX 255  //limit for the integral term
  #define K1 0.95 //smoothing factor within the PID
  #define PID_dT ((OVERSAMPLENR * 10.0)/(F_CPU / 64.0 / 256.0)) //sampling period of the temperature routine
    #define  DEFAULT_Kp 22.92
    #define  DEFAULT_Ki 1.67
    #define  DEFAULT_Kd 79
#define MAX_BED_POWER 255 // limits duty cycle to bed; 255=full current
#define PREVENT_DANGEROUS_EXTRUDE
#define PREVENT_LENGTHY_EXTRUDE
#define EXTRUDE_MINTEMP 170
#define EXTRUDE_MAXLENGTH (X_MAX_LENGTH+Y_MAX_LENGTH) //prevent extrusion of very large distances.
#define ENDSTOPPULLUPS // Comment this out (using // at the start of the line) to disable the endstop pullup resistors
  #define ENDSTOPPULLUP_XMAX
  #define ENDSTOPPULLUP_YMAX
  #define ENDSTOPPULLUP_ZMAX
  #define ENDSTOPPULLUP_XMIN
  #define ENDSTOPPULLUP_YMIN
  #define ENDSTOPPULLUP_ZMIN
const bool X_MIN_ENDSTOP_INVERTING = true; // set to true to invert the logic of the endstop.
const bool Y_MIN_ENDSTOP_INVERTING = true; // set to true to invert the logic of the endstop.
const bool Z_MIN_ENDSTOP_INVERTING = false; // set to true to invert the logic of the endstop.
const bool X_MAX_ENDSTOP_INVERTING = false; // set to true to invert the logic of the endstop.
const bool Y_MAX_ENDSTOP_INVERTING = false; // set to true to invert the logic of the endstop.
const bool Z_MAX_ENDSTOP_INVERTING = false; // set to true to invert the logic of the endstop.
#if defined(COREXY) && !defined(DISABLE_MAX_ENDSTOPS)
  #define DISABLE_MAX_ENDSTOPS
#endif
#define X_ENABLE_ON 0
#define Y_ENABLE_ON 0
#define Z_ENABLE_ON 0
#define E_ENABLE_ON 0 //For all extruders
#define DISABLE_X false
#define DISABLE_Y false
#define DISABLE_Z false
#define DISABLE_E false // For all extruders
#define DISABLE_INACTIVE_EXTRUDER true //disable only inactive extruders and keep active extruder enabled
#define INVERT_X_DIR true    // for Mendel set to false, for Orca set to true
#define INVERT_Y_DIR true    // for Mendel set to true, for Orca set to false
#define INVERT_Z_DIR true    // for Mendel set to false, for Orca set to true
#define INVERT_E0_DIR false   // for direct drive extruder v9 set to true, for geared extruder set to false
#define INVERT_E1_DIR false   // for direct drive extruder v9 set to true, for geared extruder set to false
#define INVERT_E2_DIR false   // for direct drive extruder v9 set to true, for geared extruder set to false
#define X_HOME_DIR 1
#define Y_HOME_DIR 1
#define Z_HOME_DIR 1
#define min_software_endstops true // If true, axis won't move to coordinates less than HOME_POS.
#define max_software_endstops true  // If true, axis won't move to coordinates greater than the defined lengths below.
#define X_MAX_POS DELTA_PRINTABLE_RADIUS + 15 //need this for z-probe retraction
#define X_MIN_POS -DELTA_PRINTABLE_RADIUS
#define Y_MAX_POS DELTA_PRINTABLE_RADIUS
#define Y_MIN_POS -DELTA_PRINTABLE_RADIUS
#define Z_MAX_POS MANUAL_Z_HOME_POS
#define Z_MIN_POS 0
#define X_MAX_LENGTH (X_MAX_POS - X_MIN_POS)
#define Y_MAX_LENGTH (Y_MAX_POS - Y_MIN_POS)
#define Z_MAX_LENGTH (Z_MAX_POS - Z_MIN_POS)
#define ENABLE_AUTO_BED_LEVELING // Delete the comment to enable (remove // at the start of the line)
#define Z_PROBE_REPEATABILITY_TEST  // If not commented out, Z-Probe Repeatability test will be included if Auto Bed Leveling is Enabled.
  #define AUTO_BED_LEVELING_GRID
    #define DELTA_PROBABLE_RADIUS (DELTA_PRINTABLE_RADIUS-15)
    #define LEFT_PROBE_BED_POSITION -DELTA_PROBABLE_RADIUS
    #define RIGHT_PROBE_BED_POSITION DELTA_PROBABLE_RADIUS
    #define BACK_PROBE_BED_POSITION DELTA_PROBABLE_RADIUS
    #define FRONT_PROBE_BED_POSITION -DELTA_PROBABLE_RADIUS
    #define AUTO_BED_LEVELING_GRID_POINTS 7
    #define AUTO_BED_LEVELING_GRID_X ((RIGHT_PROBE_BED_POSITION - LEFT_PROBE_BED_POSITION) / (AUTO_BED_LEVELING_GRID_POINTS - 1))
    #define AUTO_BED_LEVELING_GRID_Y ((BACK_PROBE_BED_POSITION - FRONT_PROBE_BED_POSITION) / (AUTO_BED_LEVELING_GRID_POINTS - 1))
    #define NONLINEAR_BED_LEVELING
  #define X_PROBE_OFFSET_FROM_EXTRUDER 20.0
  #define Y_PROBE_OFFSET_FROM_EXTRUDER -12.2
  #define Z_PROBE_OFFSET_FROM_EXTRUDER -7.15  //WAS 7.0 Increase this if the first layer is too thin.
  #define Z_RAISE_BEFORE_HOMING 4       // (in mm) Raise Z before homing (G28) for Probe Clearance.
  #define XY_TRAVEL_SPEED 8000         // X and Y axis travel speed between probes, in mm/min
  #define Z_RAISE_BEFORE_PROBING 20  //How much the extruder will be raised before traveling to the first probing point.
  #define Z_RAISE_BETWEEN_PROBINGS 5  //How much the extruder will be raised when traveling from between next probing points
  #define Z_PROBE_RETRACT_SCREW_X 82.5
  #define Z_PROBE_RETRACT_SCREW_Y 16.5
  #define Z_PROBE_RETRACT_SCREW_Z 36.0
  #define Z_PROBE_RETRACT_DOWN 23.0 // (in mm) how much to move down to retract the probe
  #define Z_SAFE_HOMING   // This feature is meant to avoid Z homing with probe outside the bed area.
    #define Z_SAFE_HOMING_X_POINT (X_MAX_LENGTH/2)    // X point for Z homing when homing all axis (G28)
    #define Z_SAFE_HOMING_Y_POINT (Y_MAX_LENGTH/2)    // Y point for Z homing when homing all axis (G28)
#define MANUAL_HOME_POSITIONS  // If defined, MANUAL_*_HOME_POS below will be used
#define BED_CENTER_AT_0_0  // If defined, the center of the bed is at (X=0, Y=0)
#define MANUAL_X_HOME_POS 0
#define MANUAL_Y_HOME_POS 0
#define MANUAL_Z_HOME_POS 230  //For delta: Distance between nozzle and print surface after homing.
#define NUM_AXIS 4 // The axis order in all axis related arrays is X, Y, Z, E
#define HOMING_FEEDRATE {100*60, 100*60, 100*60, 0}  // set the homing speeds (mm/min)
#define XYZ_FULL_STEPS_PER_ROTATION 200
#define XYZ_MICROSTEPS 16
#define XYZ_BELT_PITCH 2
#define XYZ_PULLEY_TEETH 16
#define XYZ_STEPS (XYZ_FULL_STEPS_PER_ROTATION * XYZ_MICROSTEPS / double(XYZ_BELT_PITCH) / double(XYZ_PULLEY_TEETH))
#define DEFAULT_AXIS_STEPS_PER_UNIT   {XYZ_STEPS, XYZ_STEPS, XYZ_STEPS, 155}   //E WAS 130
#define DEFAULT_MAX_FEEDRATE          {200, 200, 200, 200}    // (mm/sec)
#define DEFAULT_MAX_ACCELERATION      {9000,9000,9000,9000}    // X, Y, Z, E maximum start speed for accelerated moves. E default values are good for skeinforge 40+, for older versions raise them a lot.
#define DEFAULT_ACCELERATION          3000    // X, Y, Z and E max acceleration in mm/s^2 for printing moves
#define DEFAULT_RETRACT_ACCELERATION  3000   // X, Y, Z and E max acceleration in mm/s^2 for retracts
#define DEFAULT_XYJERK                20.0    // (mm/sec)
#define DEFAULT_ZJERK                 20.0    // (mm/sec)
#define DEFAULT_EJERK                 20.0    // (mm/sec)
#define CUSTOM_M_CODES
  #define CUSTOM_M_CODE_SET_Z_PROBE_OFFSET 851
  #define Z_PROBE_OFFSET_RANGE_MIN -15
  #define Z_PROBE_OFFSET_RANGE_MAX -5
#define PLA_PREHEAT_HOTEND_TEMP 180
#define PLA_PREHEAT_HPB_TEMP 0   //WAS 70
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

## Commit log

2016-11-22 Initial import
    [Configuration.h, Configuration_adv.h, KosselBedBracketFSR.stl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]
2016-11-25 Updates to configuration and support print plate
    [Configuration.h, plate04_support.scad, plate04_support.stl]
2016-11-29 Temporary fix for plate 04 (support)
    [plate04_support.stl]
2016-12-14 Final version of Assembly Manual HR
2016-12-16 Added Slic3r config file
    [Configuration.h]
2017-01-29 Added 3D printer cotrol basics chapter to User manual HR
2017-02-05 Added Printer Calibration chapter to User Manual HR
2017-02-06 Ramps bracket updated for better fit
    [RampsBracket.skp, RampsBracket.stl]
2017-02-06 Added simple test cube model for test printing and calibration
    [test_cube.scad, test_cube.stl]
2017-02-06 Added Z-probe Calibration chapter to User Manual HR
2017-02-09 Added 3D printing basics chapter to User Manual HR
2017-02-10 Groove mount adjusted for E3D v6 Lite hotend
    [groove_mount.scad, groove_mount_e3d.stl]
2017-02-14 Changed effector and retractable for E3D Lite update
    [effector.scad, effector.stl, groove_mount.stl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]
2017-02-18 Effector model corrections after first print
    [effector.scad]
2017-02-22 Started modelling cooling fan mount
    [chamfers.scad, part_cooling_fan_mount.scad]
2017-02-23 Moved retractable 1.5 mm out to make room for spring and terminal
    [retractable.scad, retractable.stl]
2017-02-23 Designed base part of cooling fan mount
    [part_cooling_fan_mount.scad, part_cooling_fan_mount.stl]
2017-02-25 Changed fan duct type on parts cooling fan mount
    [part_cooling_fan_mount.scad, part_cooling_fan_mount.stl]
2017-03-08 Part cooling fan mount corrections
    [part_cooling_fan_mount.scad, part_cooling_fan_mount.stl]
2017-03-09 Changed effector central hole to make collet accessible
    [effector.scad, effector.stl]
2017-03-11 Corrections to mount frame holes on extruder base
    [compact_direct_drive_extruder.scad, compact_direct_drive_extruder_base.stl]
2017-03-16 Groove mount lip correction
    [groove_mount.scad, groove_mount.stl]
2017-03-25 Changes to Marlin firmware to adjust for E3D Lite hotend
    [Configuration.h]
2017-04-14 A little bit shorter part cooling fan
    [part_cooling_fan_mount.scad, part_cooling_fan_mount.stl]
2017-05-05 E steps value for E3D added to configuration
    [Configuration.h]
2017-05-24 Extended fan duct on part cooling fan mount
    [part_cooling_fan_mount.scad]
2017-05-26 Second version of part cooling fan mount's duct
    [part_cooling_fan_mount.scad]
2017-05-30 Different version of part cooling fan mount
    [part_cooling_fan_mount.scad]
2017-06-09 Longer arm for part cooling fan mount v2
    [part_cooling_fan_mount.scad]
2017-06-13 Increased MANUAL_Z_HOME because of autoleveling problems, set default baudrate to 115200
    [Configuration.h]
2017-09-21 Extended part cooling fan mount and hook clip to fit 1.1 version
    [clip.scad, part_cooling_fan_mount.scad]
2017-09-21 Started working on new ramps bracket model
    [ramps_bracket.scad]
2017-09-29 Ramps bracket full model ready for test print
    [ramps_bracket.scad]
2017-10-10 Fixed NEMA mount holes
    [compact_direct_drive_extruder.scad, compact_direct_drive_extruder.stl]
2017-10-10 Started new bed bracket in openscad
    [bed_bracket.scad, ramps_bracket.stl]
2017-11-16 Final version of bed bracket
    [bed_bracket.scad]
2017-11-16 Lower baudrate, bed leveling from 5 to 7 grid, minor chanfes to geometry params
    [Configuration.h]
2017-11-16 Models clenup
    [KosselBedBracketFSR.stl, RampsBracket.skp, RampsBracket.stl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]
2017-11-16 Updated print plate 03
    [bed_bracket.scad, plate03_3x.scad, plate03_3x.stl]
2017-12-05 New Assembly manuals for version 1.1
2017-12-26 Added support for connector plate model (power part)
    [connector_plate.scad, connector_plate_power.stl, plate04_support.scad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]
